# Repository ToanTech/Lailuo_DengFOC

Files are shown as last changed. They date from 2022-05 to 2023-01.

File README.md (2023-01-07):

# DengFOC莱洛LQR自平衡三角形项目
**DengFOC莱洛LQR自平衡三角形**是基于45同学开源的[莱洛三角形项目](https://gitee.com/coll45/foc)，进行结构改进和效果优化后应用在我开源的[DengFOC](https://github.com/ToanTech/Deng-s-foc-controller)双路无刷电机驱动器上的DengFOC配套项目。

**项目完全开源，你可以根据本Github内容自行白嫖，或者，支持一下灯哥的辛勤劳作，进入灯哥开源TB店购买DengFOC莱洛自平衡三角形套件，一键配齐。**

[DengFOC动莱洛自平衡三角形套件--链接猛击(进店后在 所有宝贝 处可找到)](https://shop564514875.taobao.com/)





## 1 视频教程

配套本开源项目，灯哥精心制作了全组装过程视频教程和算法原理课，请点击查看：

[1 DengFOC LQR莱洛三角形--效果展示](https://www.bilibili.com/video/BV1Mg411o7hd/)

[2  DengFOC LQR莱洛三角形算法原理和DIY实现](https://www.bilibili.com/video/BV1QG4y1Y76f/)

## 2 接线

只要你手头有一块DengFOC V3（你可以在TB搜索**灯哥开源**进入店铺购买，或根据[DengFOC开源仓库](https://github.com/ToanTech/Deng-s-foc-controller)的开源资料自制）就可以快速搭接出此项目，项目供电默认电压为12V(3S航模电池)，除DengFOC外，其它电子元器件主要由一个2204无刷电机，两个 AS5600 编码器，一个 MPU6050 组成。其接线表格如下,其中，接线位置指的是DengFOC无刷驱动板上的针脚位置：

| 零件 | 接线位置 |
| --- | --- |
| 2204电机 | DengFOC M0位置（无刷电机0） |
| AS5600 | SDA0,SCL0,3V3,GND |
| MPU6050  | SDA1,SCL1,3V3,GND |

<div align=center>&width=540"</div>

如果你是自行DIY，那么按照上面的接线表格将线接入DengFOC即可；如果你是采用在 [灯哥开源 淘宝店](https://shop564514875.taobao.com/) 购买的莱洛三角形套件，那么你会得到**如下图所示配套线材**。

配套的接线材料有：两套接线，一套是AS5600的线，一头是杜邦端子，接有两根黑线GND，一根红线VCC，一根绿线SDA，一根黄线SCL；另一端是两个3p端子，其中一个3p端子接绿色SDA，黄色SCL，黑色DIR；另一个是接红色VCC，黑色GND，如下图中左边的线所示。

另一套是MPU6050的线，一头是杜邦端子，接有一根黑线GND，一根红线VCC，一根黄线SCL，一根绿线SDA；另一端接一个4p端子），如下图中右边的线：

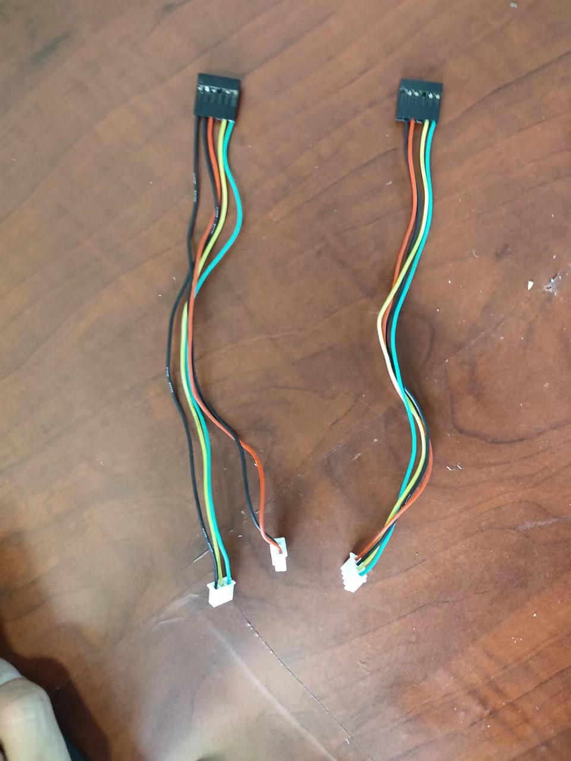
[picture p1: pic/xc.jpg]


### 2.1 对于 AS5600

首先，将上图左边的线按照下图所示穿过三角块和底板打印件：

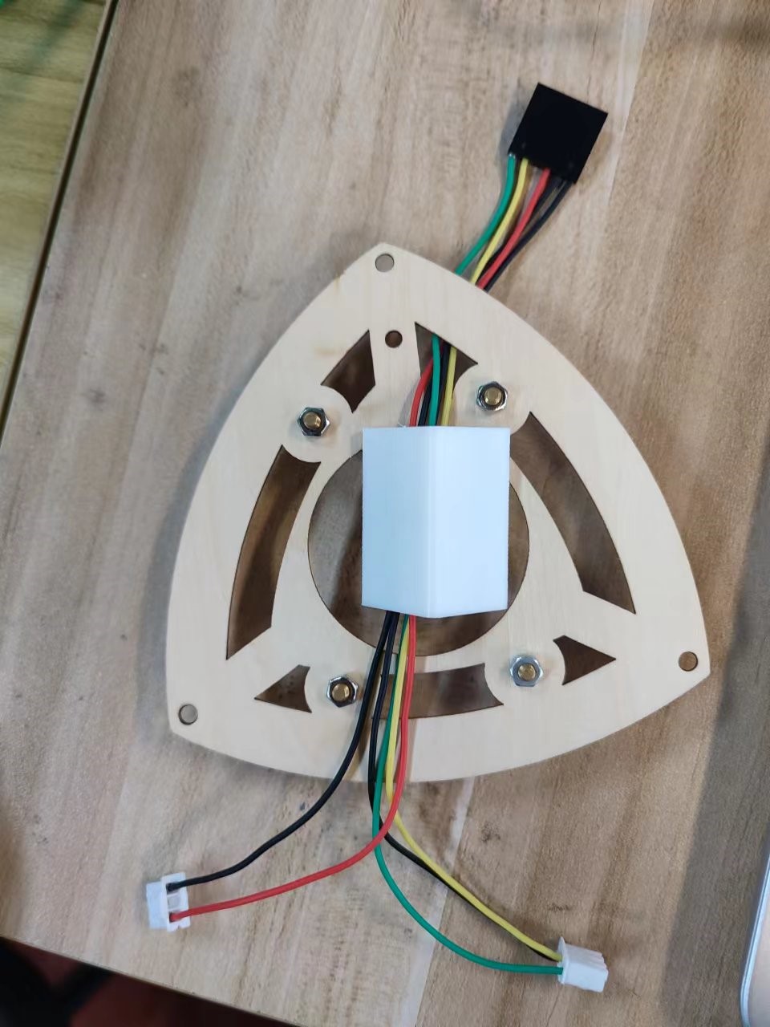
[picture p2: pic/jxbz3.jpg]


接着，将线的其中一个3p端子接GND、SCL和SDA线，其中GND为黑色线，SCL为黄色线，SDA为绿色线；另一个只连着两条线的端子用来接VCC和GND，VCC为红色线，GND为黑色线。接线位置如下图所示：

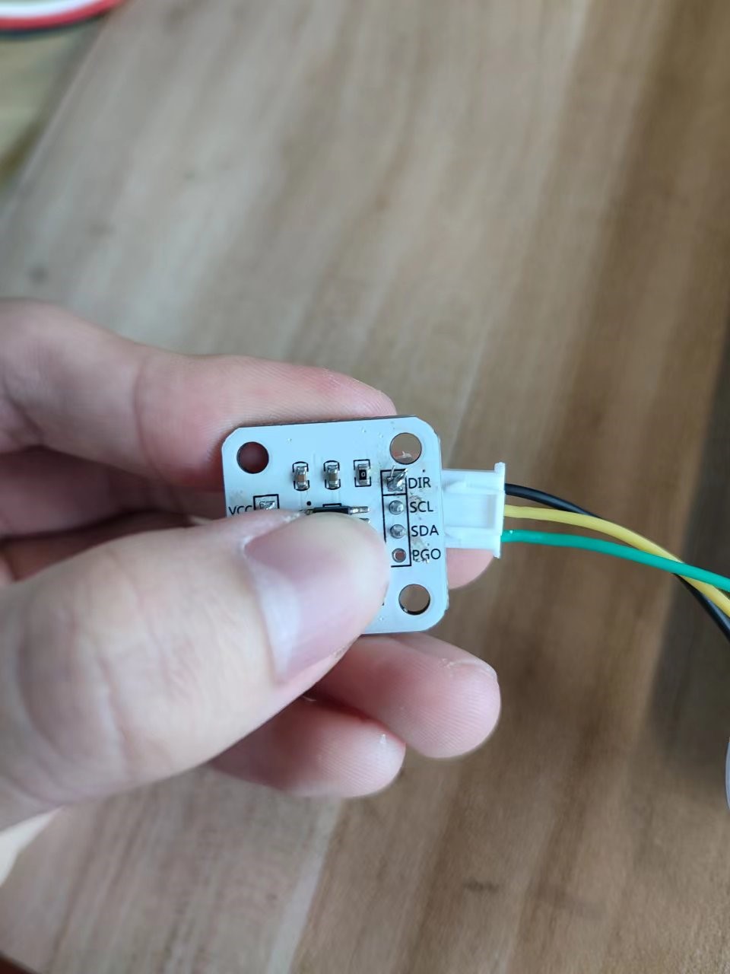
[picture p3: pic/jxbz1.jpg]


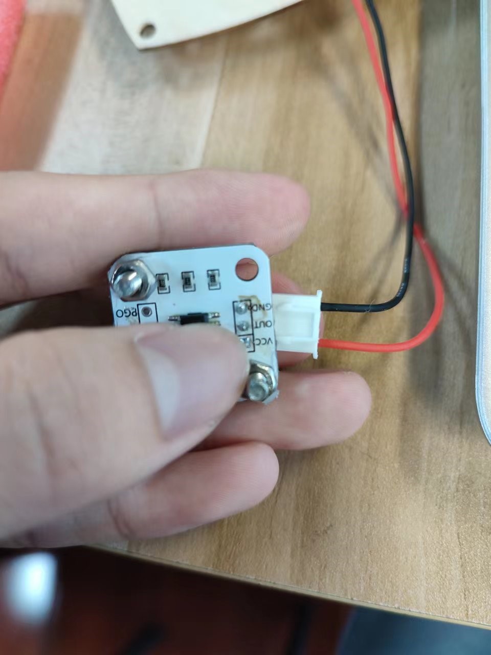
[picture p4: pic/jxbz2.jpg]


最后，将杜邦线的另一端按照下图的顺序接在DengFOC的杜邦端口上：

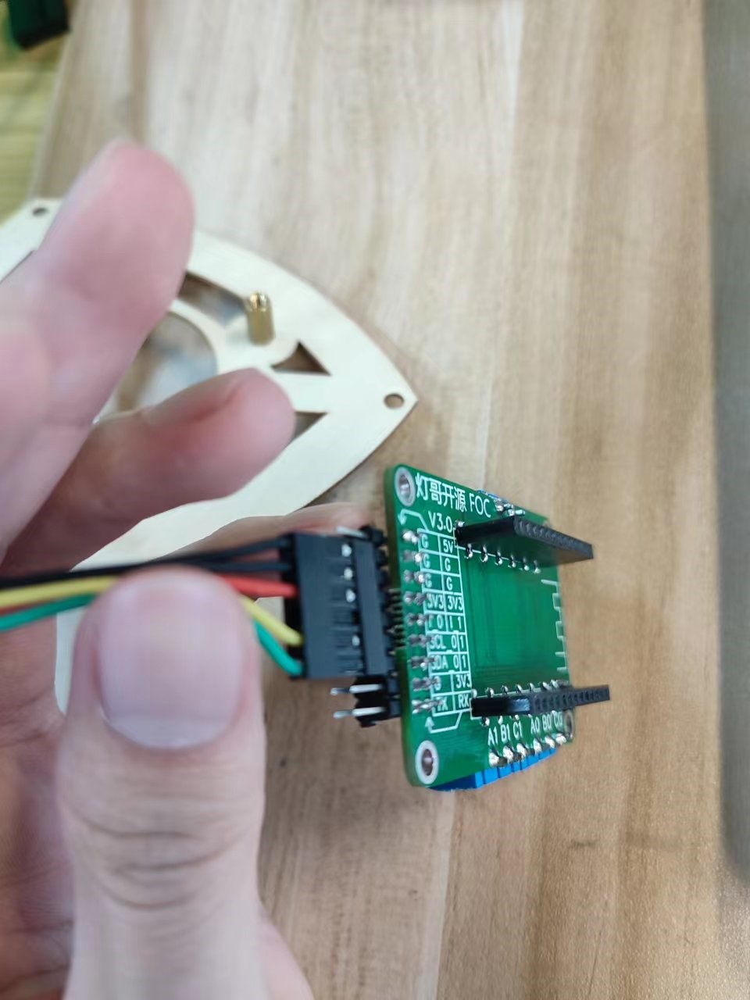
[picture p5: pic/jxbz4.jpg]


这就是AS5600的接线过程。

### 2.2 对于MPU6050

首先，将MPU6050的四根线穿过三角块和底板打印件，如下图所示：

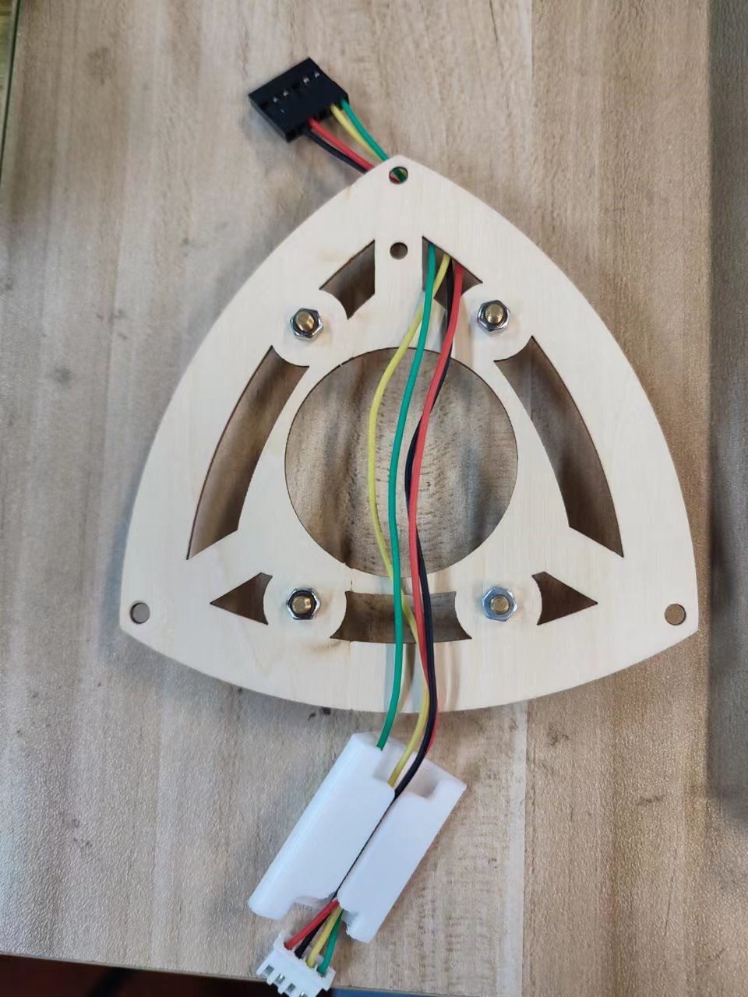
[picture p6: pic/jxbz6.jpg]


将4P端子按下图的顺序接SDA，SCL，GND,VCC线，SDA为绿色线， SCL为黄色线，GND为黑色线，VCC为红色线

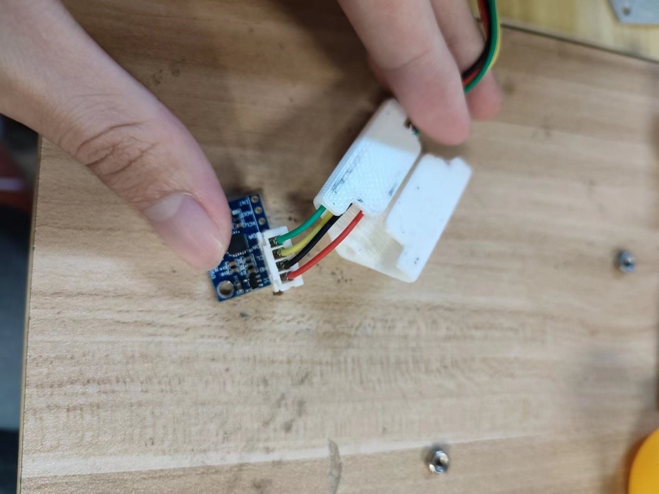
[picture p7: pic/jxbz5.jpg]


再将杜邦线的另一端按照下图的顺序接在杜邦端口：

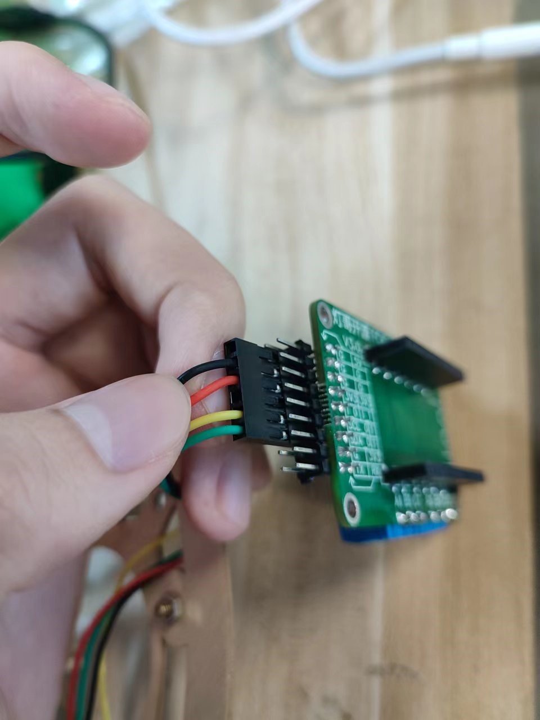
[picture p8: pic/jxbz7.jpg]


这就是MPU6050的接线步骤

### 2.3 对于电机

直接接到电机M0接口（无刷电机0）接口即可，若接入后，在调试过程中发现动量轮不能减小误差，反而会加剧误差的话，证明电机转向接反，此时对调电机其中两根相线即可。

## 3 零件制造

莱洛三角形的由两种DIY方式，一个是**3D打印版本**；一个是**激光切割的木材板版本**

**对于3D打印版本**：主要零件为3D打印，下载文件夹中的图纸，全100%密度打印即可。

**对于激光切割的木材版版本**：底板为激光切割，固定三角型为3D打印，下载文件夹中的图纸，对应进行切割和打印即可。

零件打印图纸和木材板切割图纸都可以在本项目的开源文件夹中找到。

## 4 下载程序

下载项目文件夹中的 lailuo.ino 程序，用Arduino IDE打开，用串口连接DengFOC，即可按照与一般Arduino一致的方法上传。

## 5 调试

在安装好机械结构后，本莱洛三角形的调试可以采用45同学开发的调试工具进行调试，调试步骤如下：

打开 **调试上位机** 中自带的可执行文件_main文件夹，点击main.exe文件进入交互界面:

ts1

ts1

进入之后的界面如下：

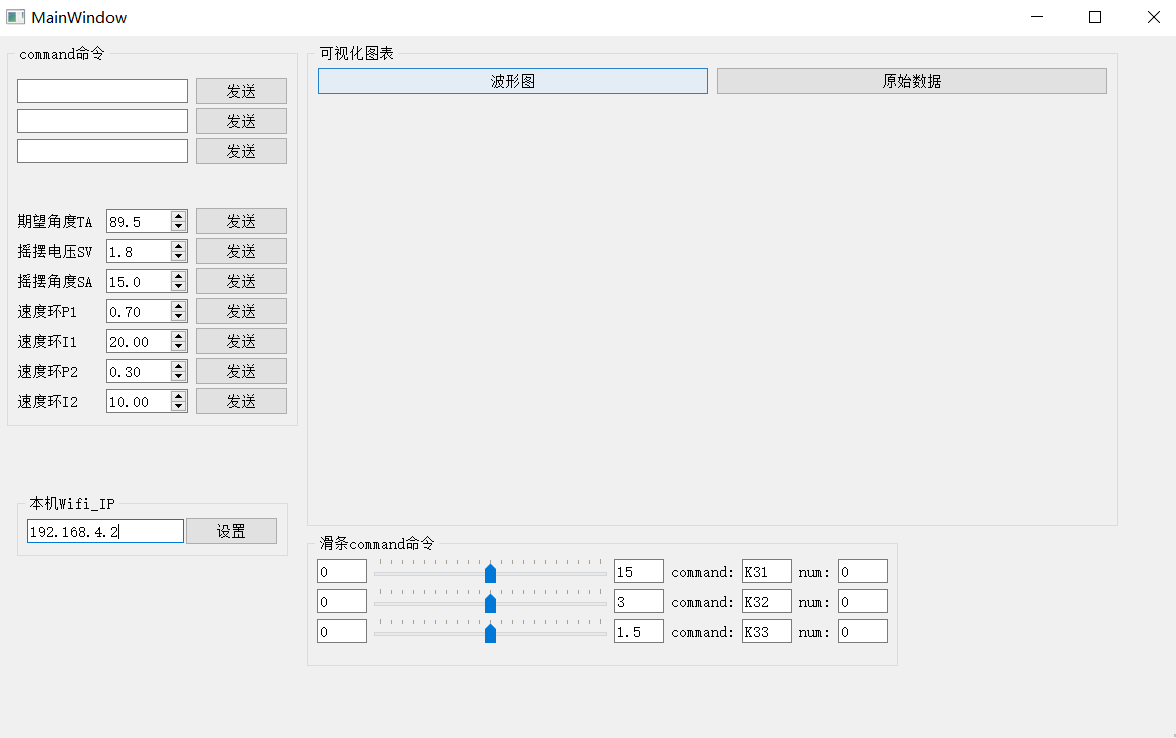
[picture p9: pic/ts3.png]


要使用这个调试软件，首先要先将莱洛三角形上电，然后在WiFi列表中找到**esp32_lailuo**这个WiFi，并连接（WiFi密码可以在源程序中找到）。

ts1

已经连接WiFi之后点击设置键，就可以开始调试了。

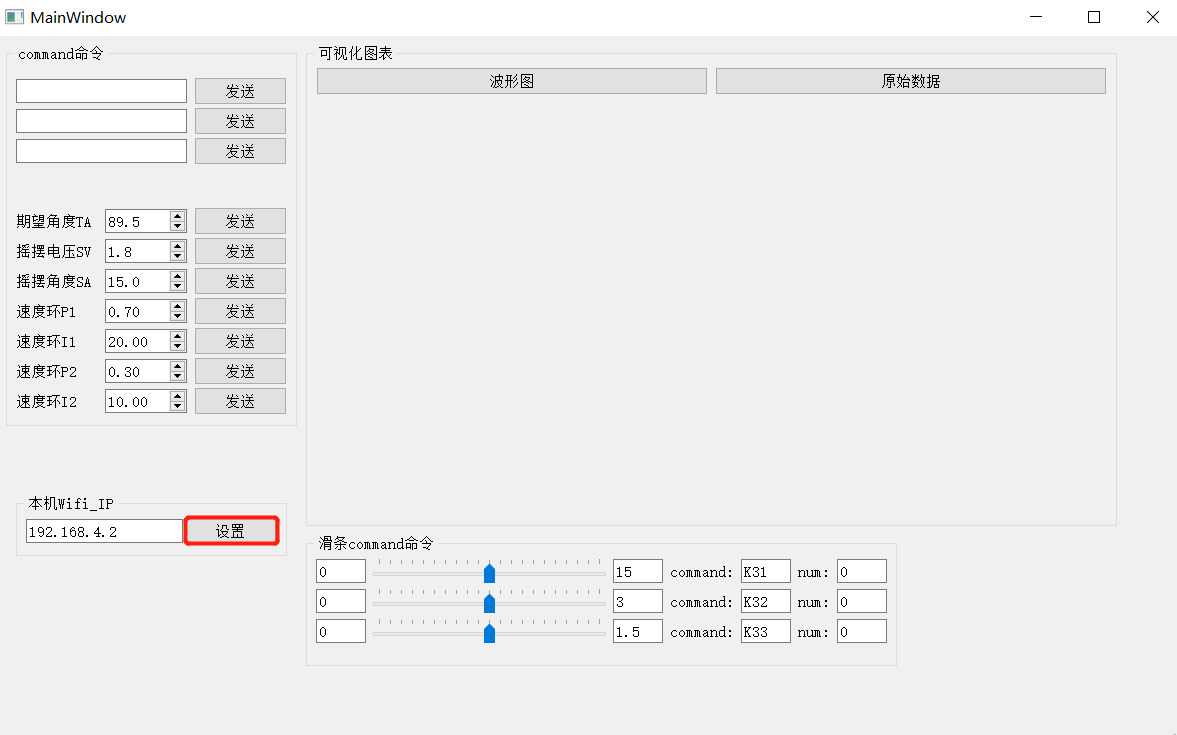
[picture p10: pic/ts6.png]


点击设置按键后，软件自动与DengFOC通讯，得到界面如下：

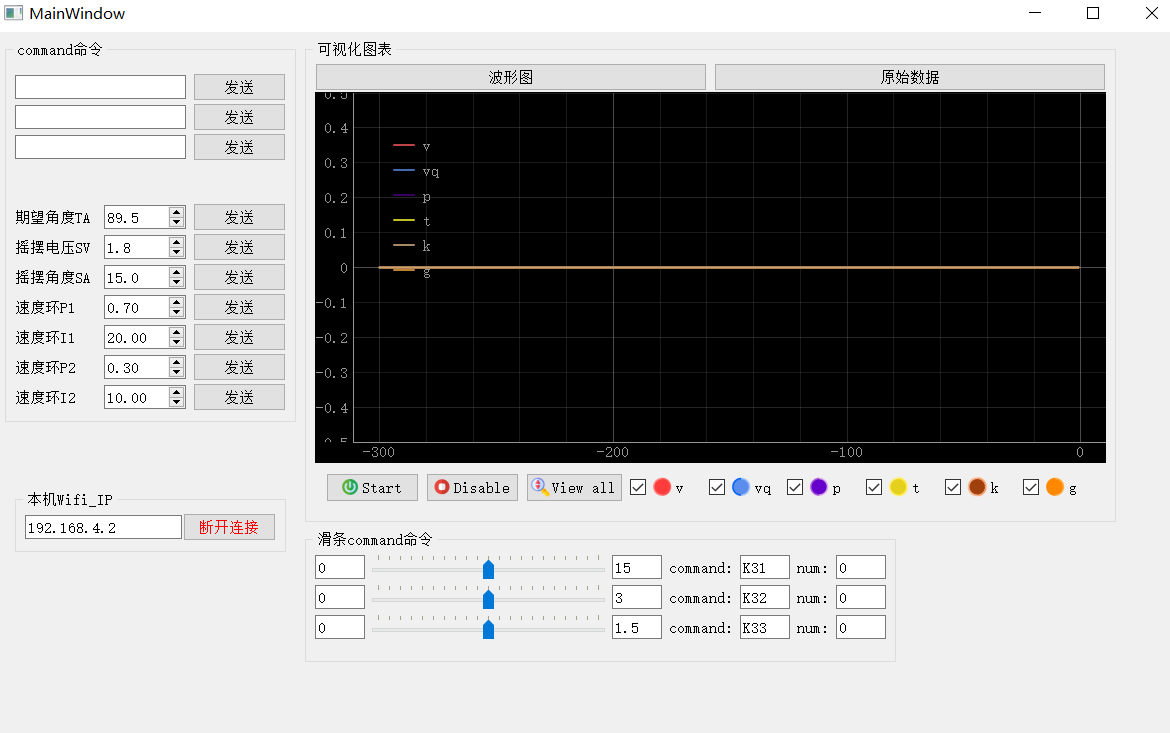
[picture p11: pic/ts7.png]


其中：

**Start**：可以在可视化图表显示各个参数的波形。

**Disable**：按下后会变成Enable，是用来打开或者关闭电机的按钮，这个在调参时可以用于开启和关闭电机，防止电机在不需要的时候乱动。

**View all**：如果你放大了波形图然后想让波形图的大小恢复原样，就可以点击这个按钮。

在调试时，我们先点击 **Start** 按键，使得软件将点击的参数显示出来，接着，点击**Disable**先禁止电机，防止电机乱动影响调试观测。在完成这一步后，下图便是调试时需要操作主要界面部分：

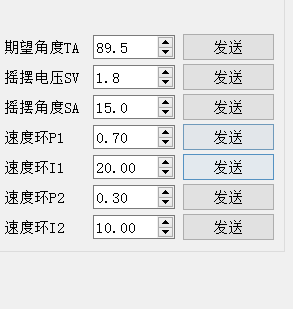
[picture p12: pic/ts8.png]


期望角度就是他设置的平衡时的角度，在调试时，我们需要将莱洛三角形扶起，使它保持垂直于桌面，如下图所示：

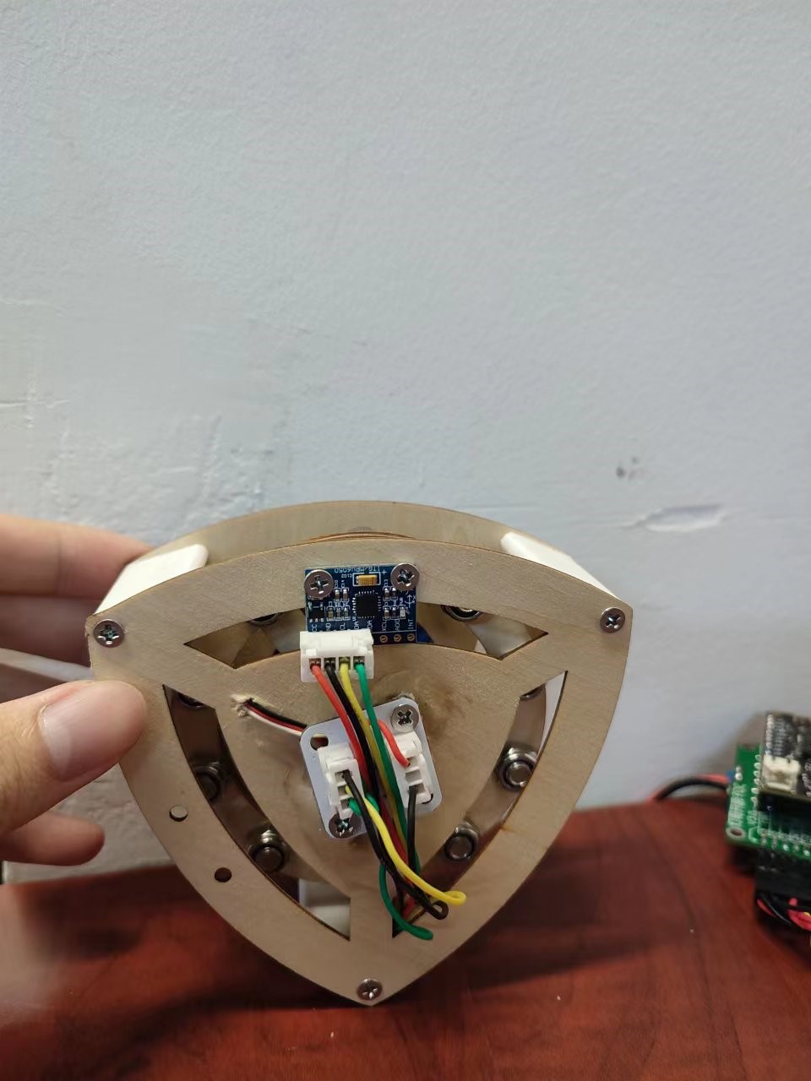
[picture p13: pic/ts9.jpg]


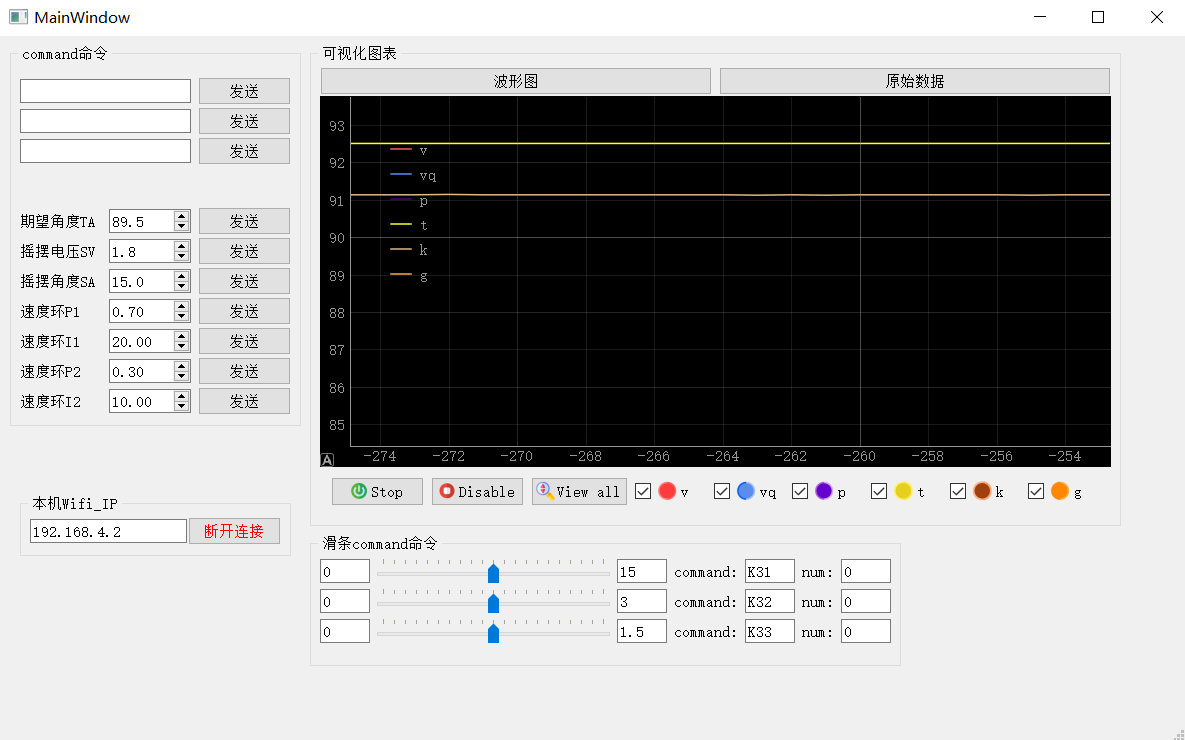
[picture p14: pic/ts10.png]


如上图，黄色波形所显示的就是莱洛三角形当前储存的期望角度，橙色的波形就是目前所在的角度，将软件中的**期望角度**设置为橙色的角度后，就完成了莱洛三角形的角度标定。

摇摆电压控制的是莱洛三角形左右摇摆的电压，电压越大就能经过越少次摆动到达平衡，但是摇摆电压过大会翻跟头。

摇摆角度是离平衡状态还差多少度时，切换到自平衡控制。

理论上，你只需要设置好**期望角度**，即可正常使用该莱洛三角形，其它的参数如摇摆电压，摇摆角度等，在程序中已经预设了我们调到的最佳参数值，除非更改机械结构或特殊情况，否则无需设置。

完成设置好**期望角度**之后，电机电机的状态按钮，使其由**Disable**变为**Ensable**，此时电机开始转动，在你设置的期望角度处将为自动自平衡稳当当的立住。

如果此时将莱洛三角形推倒，莱洛三角形将会摇晃，并努力使得自己回到能够自稳定的位置，当到达能自稳定的位置后，三角形将重新自平衡立住。

## 6 其它注意事项

如果更换为其他电机，需要重新设置电机极对数

如果自稳效果与倾倒方向相反，证明电机三相线接反，导致电机转向接反，调换三相线中其中两根即可

## 7 致谢

感谢 45 同学开源的[莱洛三角形项目](https://gitee.com/coll45/foc)，也感谢他在我将莱洛三角形项目应用在 DengFOC 过程中所给予的支持。

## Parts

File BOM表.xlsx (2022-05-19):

电控 |  |  | 机械
零件名称 | 数量 | 备注 | 零件名称 | 数量
DengFOC | 1 |  | 木底板1 | 1
MPU6050 | 1 |  | 木底板2 | 1
AS5600 | 1 |  | 三角块打印件 | 3
配套传感器径向磁铁 | 1 |  | 6701ZZ轴承 | 2
2204云台电机 | 1 | 电机TB地址：https://item.taobao.com/item.htm?id=647180650088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 | M3x10螺丝 | 10
AS5600杜邦线 | 红色VCC*1 |  | M2.5*4螺丝 | 4
 | 黑色GND*2 |  | 单通M3*10mm | 4
 | 黄色SCL*1 |  | M3螺母 | 6
 | 绿色SDA*1 |  | 双通M3*4铜柱 | 2
MPU6050杜邦线 | 红色VCC*1 |  | m2.5*6螺丝 | 4
 | 黑色GND*1
 | 黄色SCL*1
 | 绿色SDA*1
4S电池 | 1

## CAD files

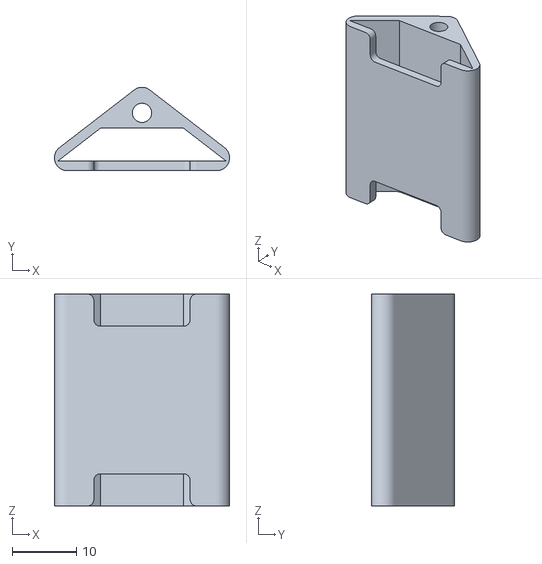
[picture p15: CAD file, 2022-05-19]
机械结构/3D打印版/triangle_bar_4.stl
27.3 x 13.0 x 33.0

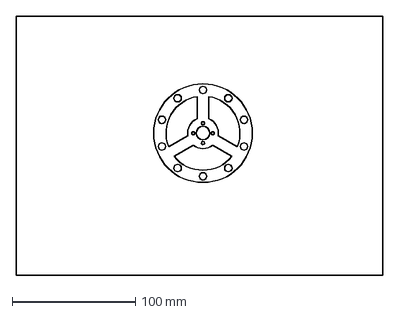
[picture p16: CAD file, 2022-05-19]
机械结构/木材版/lun1.dxf
297.0 x 210.0 mm

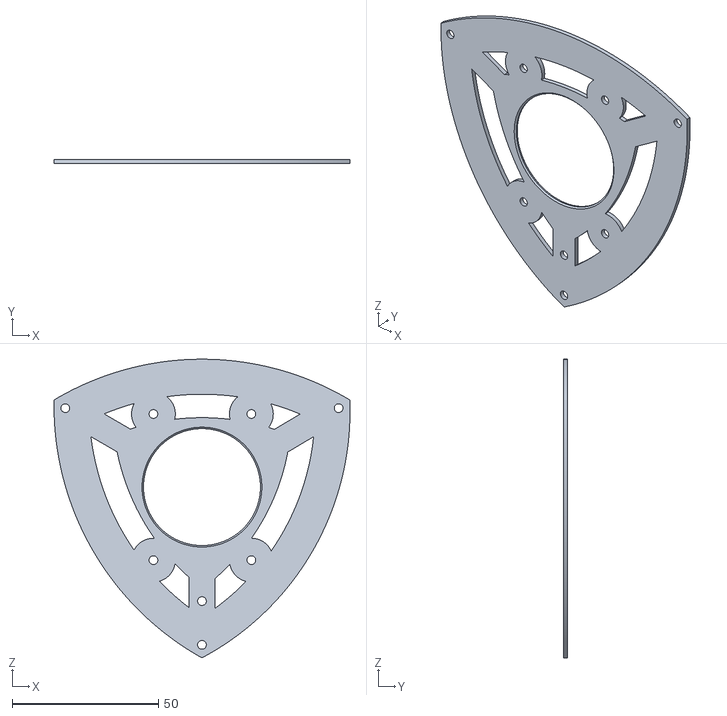
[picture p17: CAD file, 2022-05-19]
机械结构/3D打印版/lailuo_base2_19.stl
101.3 x 1.50 x 102.2

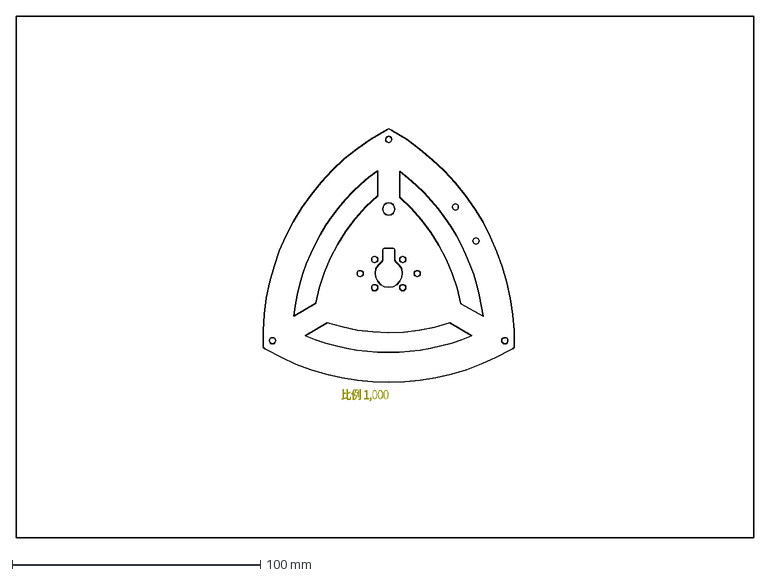
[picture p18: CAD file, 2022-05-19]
机械结构/木材版/ban2.dxf
比例 1,000

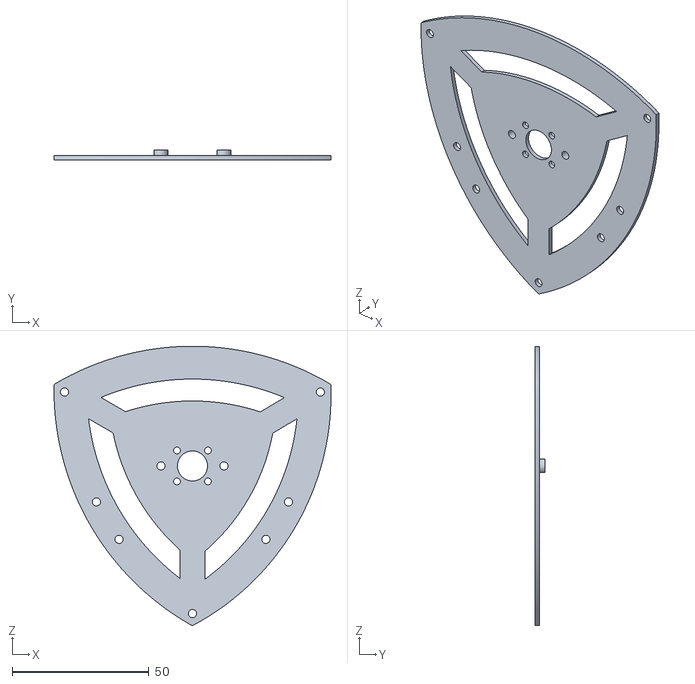
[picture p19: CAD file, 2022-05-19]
机械结构/3D打印版/lailuo_base_24.stl
101.3 x 3.50 x 102.2

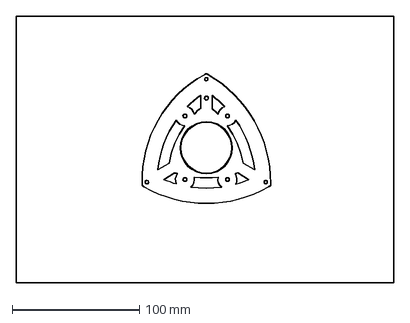
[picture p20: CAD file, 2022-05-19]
机械结构/木材版/ban1.dxf
297.0 x 210.0 mm

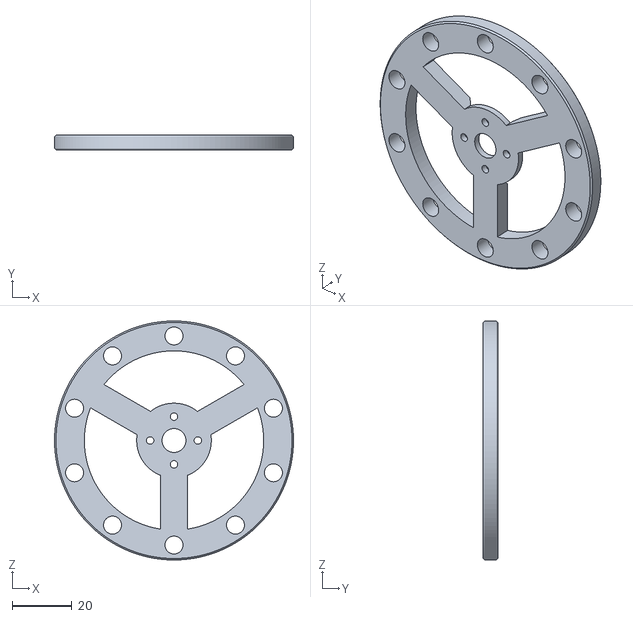
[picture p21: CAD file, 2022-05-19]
机械结构/3D打印版/centre_pan.stl
80.0 x 5.00 x 80.0

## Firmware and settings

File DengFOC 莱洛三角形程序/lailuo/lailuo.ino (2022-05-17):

  /**
arduino开发环境-灯哥开源FOChttps://gitee.com/ream_d/Deng-s-foc-controller，并安装Kalman。
FOC引脚32, 33, 25, 22    22为enable
AS5600霍尔传感器 SDA-23 SCL-5  MPU6050六轴传感器 SDA-19 SCL-18
本程序有两种平衡方式， FLAG_V为1时使用电压控制，为0时候速度控制。电压控制时LQR参数使用K1和K2，速度控制时LQR参数使用K3和K4
在wifi上位机窗口中输入：TA+角度，就可以修改平衡角度
比如让平衡角度为90度，则输入：TA90，并且会存入eeprom的位置0中 注：wifi发送命令不能过快，因为每次都会保存进eeprom
在使用自己的电机时，请一定记得修改默认极对数，即 BLDCMotor(5) 中的值，设置为自己的极对数数字，磁铁数量/2
程序默认设置的供电电压为 12V,用其他电压供电请记得修改 voltage_power_supply , voltage_limit 变量中的值
默认PID针对的电机是 GB2204 ，使用自己的电机需要修改PID参数，才能实现更好效果
 */
#include <SimpleFOC.h>
#include "Command.h"
#include <WiFi.h>
#include <AsyncUDP.h> //引用以使用异步UDP
#include "Kalman.h" // Source: https://github.com/TKJElectronics/KalmanFilter
#include "EEPROM.h"
Kalman kalmanZ;
#define gyroZ_OFF -0.19
#define FLAG_V 0
/* ----IMU Data---- */

double accX, accY, accZ;
double gyroX, gyroY, gyroZ;
int16_t tempRaw;
bool stable = 0;
uint32_t last_unstable_time;

double gyroZangle; // Angle calculate using the gyro only
double compAngleZ; // Calculated angle using a complementary filter
double kalAngleZ;  // Calculated angle using a Kalman filter

uint32_t timer;
uint8_t i2cData[14]; // Buffer for I2C data
/* ----FOC Data---- */

// driver instance
double acc2rotation(double x, double y);
float constrainAngle(float x);
const char *ssid = "esp32_lailuo";
const char *password = "qwe12345";

bool wifi_flag = 0;
AsyncUDP udp;                     //创建UDP对象
unsigned int localUdpPort = 2333; //本地端口号
void wifi_print(char * s,double num);

MagneticSensorI2C sensor = MagneticSensorI2C(AS5600_I2C);
TwoWire I2Ctwo = TwoWire(1);
LowPassFilter lpf_throttle{0.00};

//倒立摆参数
float LQR_K1_1 = 4;  //摇摆到平衡
float LQR_K1_2 = 1.5;   //
float LQR_K1_3 = 0.30; //

float LQR_K2_1 = 3.49;   //平衡态
float LQR_K2_2 = 0.26;   //
float LQR_K2_3 = 0.15; //

float LQR_K3_1 = 10;   //摇摆到平衡
float LQR_K3_2 = 1.7;   //
float LQR_K3_3 = 1.75; //

float LQR_K4_1 = 2.4;   //摇摆到平衡
float LQR_K4_2 = 1.5;   //
float LQR_K4_3 = 1.42; //

//电机参数
BLDCMotor motor = BLDCMotor(7);
BLDCDriver3PWM driver = BLDCDriver3PWM(32, 33, 25, 22);
float target_velocity = 0;
float target_angle = 90.7;
float target_voltage = 0;
float swing_up_voltage = 1.8;
float swing_up_angle = 15;
float v_i_1 = 11; // 非自稳状态
float v_p_1 = 0.56; // 非自稳状态
float v_i_2 = 9; // 自稳状态
float v_p_2 = 0.24; // 自稳状态
//命令设置
Command comm;
bool Motor_enable_flag = 0;
void do_TA(char* cmd) { comm.scalar(&target_angle, cmd);EEPROM.writeFloat(0, target_angle); }
void do_SV(char* cmd) { comm.scalar(&swing_up_voltage, cmd); EEPROM.writeFloat(4, swing_up_voltage); }
void do_SA(char* cmd) { comm.scalar(&swing_up_angle, cmd);EEPROM.writeFloat(8, swing_up_angle); }

void do_START(char* cmd) {  wifi_flag = !wifi_flag; }
void do_MOTOR(char* cmd)
{  
  if(Motor_enable_flag)
    digitalWrite(22,HIGH);
  else 
    digitalWrite(22,LOW);
  Motor_enable_flag = !Motor_enable_flag;
}
#if FLAG_V
void do_K11(char* cmd) { comm.scalar(&LQR_K1_1, cmd); }
void do_K12(char* cmd) { comm.scalar(&LQR_K1_2, cmd); }
void do_K13(char* cmd) { comm.scalar(&LQR_K1_3, cmd); }
void do_K21(char* cmd) { comm.scalar(&LQR_K2_1, cmd); }
void do_K22(char* cmd) { comm.scalar(&LQR_K2_2, cmd); }
void do_K23(char* cmd) { comm.scalar(&LQR_K2_3, cmd); }
#else
void do_vp1(char* cmd) { comm.scalar(&v_p_1, cmd); EEPROM.writeFloat(12, v_p_1);}
void do_vi1(char* cmd) { comm.scalar(&v_i_1, cmd);EEPROM.writeFloat(16, v_p_1); }
void do_vp2(char* cmd) { comm.scalar(&v_p_2, cmd); EEPROM.writeFloat(20, v_p_2);}
void do_vi2(char* cmd) { comm.scalar(&v_i_2, cmd);EEPROM.writeFloat(24, v_i_2); }
void do_tv(char* cmd) { comm.scalar(&target_velocity, cmd); }
void do_K31(char* cmd) { comm.scalar(&LQR_K3_1, cmd); }
void do_K32(char* cmd) { comm.scalar(&LQR_K3_2, cmd); }
void do_K33(char* cmd) { comm.scalar(&LQR_K3_3, cmd); }
void do_K41(char* cmd) { comm.scalar(&LQR_K4_1, cmd); }
void do_K42(char* cmd) { comm.scalar(&LQR_K4_2, cmd); }
void do_K43(char* cmd) { comm.scalar(&LQR_K4_3, cmd); }
#endif


void onPacketCallBack(AsyncUDPPacket packet)
{
  char* da;
  da= (char*)(packet.data());
  Serial.println(da);
  comm.run(da);
  EEPROM.commit();
//  packet.print("reply data");
}
// instantiate the commander
void setup() {
   Serial.begin(115200);
   if (!EEPROM.begin(1000)) {
    Serial.println("Failed to initialise EEPROM");
    Serial.println("Restarting...");
    delay(1000);
    ESP.restart();
  }

   //命令设置
 comm.add("TA",do_TA);
  comm.add("START",do_START);
   comm.add("MOTOR",do_MOTOR);
    comm.add("SV",do_SV);
    comm.add("SA",do_SA);
    target_angle = EEPROM.readFloat(0);
swing_up_voltage = EEPROM.readFloat(4);
swing_up_angle = EEPROM.readFloat(8);
#if FLAG_V
  comm.add("K11",do_K11);
  comm.add("K12",do_K12);
  comm.add("K13",do_K13);
  comm.add("K21",do_K21);
  comm.add("K22",do_K22);
  comm.add("K23",do_K23);
#else
  comm.add("VP1",do_vp1);
  comm.add("VI1",do_vi1);
  comm.add("VP2",do_vp2);
  comm.add("VI2",do_vi2);
  comm.add("TV",do_tv);
  comm.add("K31",do_K31);
  comm.add("K32",do_K32);
  comm.add("K33",do_K33);
  comm.add("K41",do_K41);
  comm.add("K42",do_K42);
  comm.add("K43",do_K43);
  v_p_1 = EEPROM.readFloat(12);
  v_i_1 = EEPROM.readFloat(16);
  v_p_2 = EEPROM.readFloat(20);
  v_i_2 = EEPROM.readFloat(24);
  motor.PID_velocity.P = v_p_1;
  motor.PID_velocity.I = v_i_1;
#endif
    // kalman mpu6050 init
  Wire.begin(23, 5,400000UL);// Set I2C frequency to 400kHz
  i2cData[0] = 7;    // Set the sample rate to 1000Hz - 8kHz/(7+1) = 1000Hz
  i2cData[1] = 0x00; // Disable FSYNC and set 260 Hz Acc filtering, 256 Hz Gyro filtering, 8 KHz sampling
  i2cData[2] = 0x00; // Set Gyro Full Scale Range to ±250deg/s
  i2cData[3] = 0x00; // Set Accelerometer Full Scale Range to ±2g
  while (i2cWrite(0x19, i2cData, 4, false))
    ; // Write to all four registers at once
  while (i2cWrite(0x6B, 0x01, true))
    ; // PLL with X axis gyroscope reference and disable sleep mode

  while (i2cRead(0x75, i2cData, 1))
    ;
  if (i2cData[0] != 0x68)
  { // Read "WHO_AM_I" register
    Serial.print(F("Error reading sensor"));
    while (1)
      ;
  }

  delay(100); // Wait for sensor to stabilize

  /* Set kalman and gyro starting angle */
  while (i2cRead(0x3B, i2cData, 6))
    ;
  accX = (int16_t)((i2cData[0] << 8) | i2cData[1]);
  accY = (int16_t)((i2cData[2] << 8) | i2cData[3]);
  accZ = (int16_t)((i2cData[4] << 8) | i2cData[5]);
  double pitch = acc2rotation(accX, accY);

  kalmanZ.setAngle(pitch);
  gyroZangle = pitch;

  timer = micros();
  Serial.println("kalman mpu6050 init");

    //wifi初始化
  WiFi.mode(WIFI_AP);
   while(!WiFi.softAP(ssid, password)){}; //启动AP
    Serial.println("AP启动成功");
  while (!udp.listen(localUdpPort)) //等待udp监听设置成功
  {
  }
  udp.onPacket(onPacketCallBack); //注册收到数据包事件
  
  I2Ctwo.begin(19, 18, 400000UL);   //SDA,SCL
  sensor.init(&I2Ctwo);

  //连接motor对象与传感器对象
  motor.linkSensor(&sensor);

  //供电电压设置 [V]
  driver.voltage_power_supply = 12;
  driver.init();

  //连接电机和driver对象
  motor.linkDriver(&driver);

  //FOC模型选择
  motor.foc_modulation = FOCModulationType::SpaceVectorPWM;

  //运动控制模式设置
#if FLAG_V
  motor.controller = MotionControlType::torque;
#else
  motor.controller = MotionControlType::velocity;
    //速度PI环设置
  motor.PID_velocity.P = 0.5;
  motor.PID_velocity.I = 20;
#endif


  //最大电机限制电机
  motor.voltage_limit = 12;

  //速度低通滤波时间常数
  motor.LPF_velocity.Tf = 0.01;

  //设置最大速度限制
  motor.velocity_limit = 40;
  motor.voltage_sensor_align = 8;

  motor.useMonitoring(Serial);
  
  //初始化电机
  motor.init();

  //初始化 FOC
  motor.initFOC();

  Serial.println(F("Motor ready."));
  Serial.println(F("Set the target velocity using serial terminal:"));


}
char buf[255];
long loop_count = 0;
void loop() {
    motor.loopFOC();
  if (1)
  {
//    loop_count++ == 10
//    loop_count = 0;
  while (i2cRead(0x3B, i2cData, 14));
    accX = (int16_t)((i2cData[0] << 8) | i2cData[1]);
    accY = (int16_t)((i2cData[2] << 8) | i2cData[3]);
    accZ = (int16_t)((i2cData[4] << 8) | i2cData[5]);
    tempRaw = (int16_t)((i2cData[6] << 8) | i2cData[7]);
    gyroX = (int16_t)((i2cData[8] << 8) | i2cData[9]);
    gyroY = (int16_t)((i2cData[10] << 8) | i2cData[11]);
    gyroZ = (int16_t)((i2cData[12] << 8) | i2cData[13]);
    
    double dt = (double)(micros() - timer) / 1000000; // Calculate delta time
    timer = micros();
    
    double pitch = acc2rotation(accX, accY);
    double gyroZrate = gyroZ / 131.0; // Convert to deg/s

    kalAngleZ = kalmanZ.getAngle(pitch, gyroZrate + gyroZ_OFF, dt);
    gyroZangle += (gyroZrate + gyroZ_OFF) * dt;
    compAngleZ = 0.93 * (compAngleZ + (gyroZrate + gyroZ_OFF) * dt) + 0.07 * pitch;

    // Reset the gyro angle when it has drifted too much
    if (gyroZangle < -180 || gyroZangle > 180)
      gyroZangle = kalAngleZ;
      
  float pendulum_angle = constrainAngle(fmod(kalAngleZ,120)-target_angle);
//  FLAG_V为1时使用电压控制，为0时候速度控制
#if FLAG_V 
   if (abs(pendulum_angle) < swing_up_angle) // if angle small enough stabilize 0.5~30°,1.5~90°
   {
     target_voltage = controllerLQR(pendulum_angle, gyroZrate, motor.shaftVelocity());
//        limit the voltage set to the motor
    if (abs(target_voltage) > motor.voltage_limit * 0.7)
      target_voltage = _sign(target_voltage) * motor.voltage_limit * 0.7;
   }
    else // else do swing-up
    {    // sets 1.5V to the motor in order to swing up
        target_voltage = -_sign(gyroZrate) * swing_up_voltage;
    }

    // set the target voltage to the motor
    if (accZ < -13000 && ((accX * accX + accY * accY) > (14000 * 14000)))
    {
      motor.move(0);
    }
    else
    {
      motor.move(lpf_throttle(target_voltage));
    }

#else
if (abs(pendulum_angle) < swing_up_angle) // if angle small enough stabilize 0.5~30°,1.5~90°
   {
   target_velocity = controllerLQR(pendulum_angle, gyroZrate, motor.shaftVelocity());
  if (abs(target_velocity) > 140)
      target_velocity = _sign(target_velocity) * 140;
      motor.controller = MotionControlType::velocity;
      motor.move(target_velocity);
   }
   else // else do swing-up
    {    // sets 1.5V to the motor in order to swing up
      motor.controller = MotionControlType::torque;
        target_voltage = -_sign(gyroZrate) * swing_up_voltage;
        motor.move(target_voltage);
    }

#endif
#if 0

//Serial.print(gyroZangle);Serial.print("\t");
Serial.print(kalAngleZ);Serial.print("\t");

  Serial.print(target_voltage);Serial.print("\t");
//  Serial.print(target_velocity);Serial.print("\t");
  Serial.print(motor.shaft_velocity);Serial.print("\t");
  Serial.print(target_angle);Serial.print("\t");
  Serial.print(pendulum_angle);Serial.print("\t");
  Serial.print(gyroZrate);Serial.print("\t");
  Serial.print("\r\n");
#endif
//  motor.move(target_velocity);
  //可以使用该方法广播信息
if(wifi_flag)
{
  memset(buf, 0, strlen(buf));  
 
  wifi_print("v", motor.shaftVelocity());
  wifi_print("vq",motor.voltage.q);
  wifi_print("p",pendulum_angle);
  wifi_print("t",target_angle);
  wifi_print("k",kalAngleZ);
  wifi_print("g",gyroZrate);

  udp.writeTo((const unsigned char*)buf, strlen(buf), IPAddress(192,168,4,2), localUdpPort); //广播数据
  }
}
}
/* mpu6050加速度转换为角度
            acc2rotation(ax, ay)
            acc2rotation(az, ay) */
double acc2rotation(double x, double y)
{
  if (y < 0)
  {
    return atan(x / y) / 1.570796 * 90 + 180;
  }
  else if (x < 0)
  {
    return (atan(x / y) / 1.570796 * 90 + 360);
  }
  else
  {
    return (atan(x / y) / 1.570796 * 90);
  }
}

// function constraining the angle in between -60~60
float constrainAngle(float x)
{
  float a = 0;
  if(x < 0)
  {
      a = 120+x;
    if(a<abs(x))
      return a;
  }
  return x;
}
// LQR stabilization controller functions
// calculating the voltage that needs to be set to the motor in order to stabilize the pendulum
float controllerLQR(float p_angle, float p_vel, float m_vel)
{
  // if angle controllable
  // calculate the control law
  // LQR controller u = k*x
  //  - k = [40, 7, 0.3]
  //  - k = [13.3, 21, 0.3]
  //  - x = [pendulum angle, pendulum velocity, motor velocity]'

  if (abs(p_angle) > 2.5)
  {
    last_unstable_time = millis();
    if(stable)
    {
      target_angle = EEPROM.readFloat(0);
      stable = 0;
    }
  }
  if ((millis() - last_unstable_time) > 1000&&!stable)
  {
    target_angle = target_angle+p_angle;
    stable = 1;
  }

  //Serial.println(stable);
  float u;
#if FLAG_V
  if (!stable)
  {
    u = LQR_K1_1 * p_angle + LQR_K1_2 * p_vel + LQR_K1_3 * m_vel;
  }
  else
  {
    //u = LQR_K1 * p_angle + LQR_K2 * p_vel + LQR_K3 * m_vel;
    u = LQR_K2_1 * p_angle + LQR_K2_2 * p_vel + LQR_K2_3 * m_vel;
  }
#else
  if (!stable)
  {
    motor.PID_velocity.P = v_p_1;
    motor.PID_velocity.I = v_i_1;
    u = LQR_K3_1 * p_angle + LQR_K3_2 * p_vel + LQR_K3_3 * m_vel;
  }
  else
  {
    motor.PID_velocity.P = v_p_2;
    motor.PID_velocity.I = v_i_2;
    //u = LQR_K1 * p_angle + LQR_K2 * p_vel + LQR_K3 * m_vel;
    u = LQR_K4_1 * p_angle + LQR_K4_2 * p_vel + LQR_K4_3 * m_vel;
  }
#endif
  return u;
}
void wifi_print(char * s,double num)
{
  char str[255];
  char n[255];
  sprintf(n, "%.2f",num);
  strcpy(str,s);
  strcat(str, n);
  strcat(buf+strlen(buf), str);
  strcat(buf, ",\0");

}
